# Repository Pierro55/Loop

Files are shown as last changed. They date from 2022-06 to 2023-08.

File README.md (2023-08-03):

# Loop Automatization Mod

<p align="center">
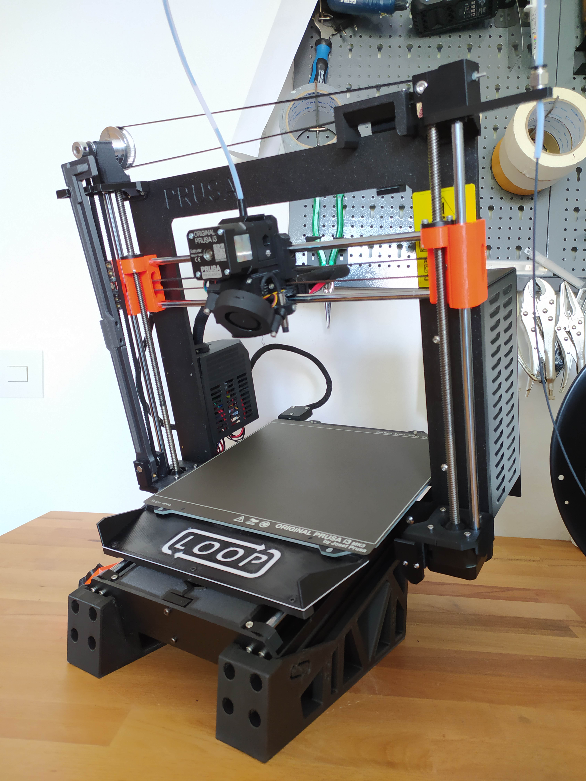
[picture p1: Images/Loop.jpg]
	
</p>

With this modification for the original Prusa MK3S+ you can put your 3D printer on autopilot and enable continuous printing. 

You can see the first version of the mechanism working in the following video:

https://user-images.githubusercontent.com/57869093/173814733-19abccf8-62e7-46f5-b48e-6825817a073e.mp4

For more detailed information check out the instruction section.

Feel free to join my Discord server for discussions and realtime updates: https://discord.gg/uEcjAfGHGe

If you are planning to build this mod, I would really appreciate it if you could post your progress on my Discord channel :)

### Credits
- Thanks to [Jonathan Kayne](https://grabcad.com/library/prusa-i3-mk3-solidworks-1) for providing the base model of the Prusa MK3
- Thanks to [smartin015](https://plugins.octoprint.org/plugins/continuousprint/) for providing the continuous print queue plugin
- Thanks to the [Octoprint team](https://octoprint.org/download/) for providing such incredible software
- I got some inspiration from [3D Que](https://www.3dque.com/) which got me motivated to build an improved system

Loop 3D printing automatisation now is integrated into [SimplyPrint](https://simplyprint.io/)

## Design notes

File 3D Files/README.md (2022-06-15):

# 3D Printing instructions
 
All STL-files are orientated in the correct orientation, just throw them into your slicer and off you go.

No support needed.

Depending on your setup (enclosure, printer on the table...) use at least PETG as material, ABS or PC would be even better.

Parts should have at leats 3-5 perimeters and 30% infill.

I printed all parts with a 0.6mm nozzle and 0.3mm layer height.

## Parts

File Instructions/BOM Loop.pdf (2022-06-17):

BOM Loop

Amount | Description | Comment | Links (DE)
2 | GT2 20T 8mm Bore Pulley | with set screws for shaft clamping | https://www.roboter-bausatz.de/p/rie (https://www.roboter-bausatz.de/p/riemenscheibe-gt2-20-zaehne-8mm-bohrung-fuer-6mm-riemen)
1 | GT2 20T Toothed Idler 5mm Bore | with bearing | https://www.roboter-bausatz.de/p/gt (https://www.roboter-bausatz.de/p/gt2-riemenscheibe-20-zaehne-5mm-bohrung-mit-dual-kugellager)
1 | GT2 60T 8mm Bore Pulley | with set screws for shaft clamping | https://www.roboter-bausatz.de/p/gt (https://www.roboter-bausatz.de/p/gt2-riemenscheibe-60-zaehne-8mm-bohrung-fuer-6mm-zahnriemen)
1 | 72cm GT2 Belt | Top Belt | https://www.roboter-bausatz.de/p/yo (https://www.roboter-bausatz.de/p/yourdroid-gt2-zahnriemen-offen-6mm-1-meter-faserverstaerkt)
1 | 69cm GT2 Belt | Belt Ejector Arm | https://www.roboter-bausatz.de/p/yo (https://www.roboter-bausatz.de/p/yourdroid-gt2-zahnriemen-offen-6mm-1-meter-faserverstaerkt)
1 | 52.5mm (stainless) steel rod | Shaft Top | https://www.dold-mechatronik.de/Pr (https://www.dold-mechatronik.de/Praezisionswelle-8mm-h6-geschliffen-und-gehaertet-Material-CF53-Zuschnitt)
1 | 31.5mm (stainless) steel rod | Shaft Bottom | https://www.dold-mechatronik.de/Pr (https://www.dold-mechatronik.de/Praezisionswelle-8mm-h6-geschliffen-und-gehaertet-Material-CF53-Zuschnitt)
1 | 62cm PTFE Tube OD 4mm | Reverse Bowden Feed-in | https://www.roboter-bausatz.de/p/1- (https://www.roboter-bausatz.de/p/1-meter-ptfe-schlauch-3-mm-x-4-mm-fuer-bowden-extruder)
1 | M6 PTFE Bowdencoupler | Reverse Bowden Feed-in, Push through type | https://www.roboter-bausatz.de/p/pc (https://www.roboter-bausatz.de/p/pc4-m6-bowden-schnellverbinder-straight-through)
17 | M3 Heat inserts | d1 Ø4,6mm; d2 Ø3,9mm; L5,7 --------------->>>>> | https://www.amazon.de/ruthex-Gewi (https://www.amazon.de/ruthex-Gewindeeinsatz-St%C3%BCck-Gewindebuchsen-Kunststoffteile/dp/B08BCRZZS3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)
5 | M3 Nut | 3x Ejector Lip + 2x Belt Idler Top
3 | M3x6 | Ejector Lip screws
14 | Button Head M3x10
1 | M3x16 | Ejector arm clamp screw
2 | M3x18 | GT2 Belt tensioner
1 | M3x30 | Top Belt Idler tensioner
1 | M5x16 | Top Belt Idler GT2 Idler "Shaft"
6 | M5x10 | Feet + Mechanics Cover
6 | Hammernut Slot 8 Type I | Feet + Mechanics Cover | https://www.ebay.de/itm/273816981 (https://www.ebay.de/itm/273816981652?var=574480277127)
1 | Square Nut M5 (8x8x2,7mm) | Top Belt Idler GT2 Idler, use some Loctite 243 to secure the bolt | https://www.ebay.de/itm/113023762 (https://www.ebay.de/itm/113023762539)
4 | Countersunk Wood screw 3x10mm | GT2 Belt tensioner --------------->>>>> | https://www.amazon.de/SPAX-Schrau (https://www.amazon.de/SPAX-Schrauben-Senkkopf-PZ-Vollgewinde-10/dp/B007259QA6)

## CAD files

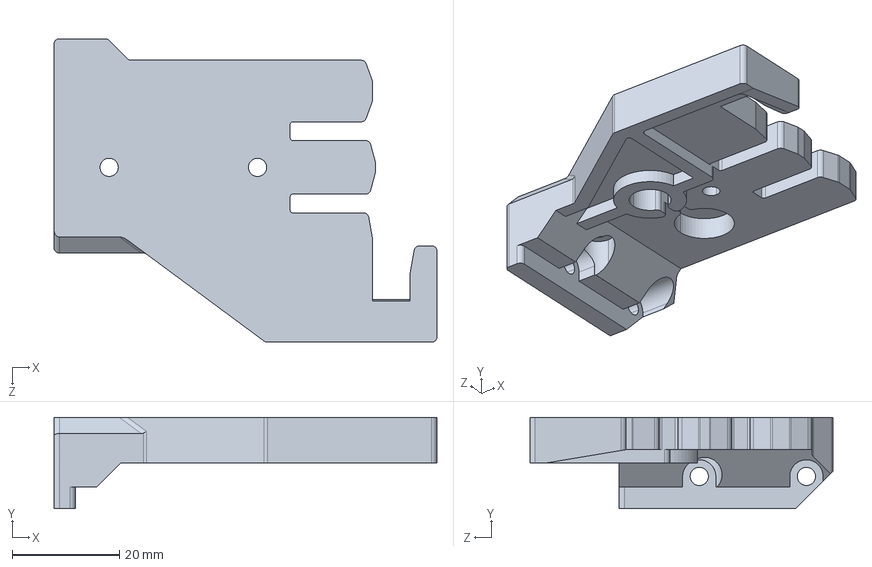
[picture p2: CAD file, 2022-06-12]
3D Files/STEP/Z_Axis_Top_LEFT.STEP
71.5 x 17.0 x 56.6 mm

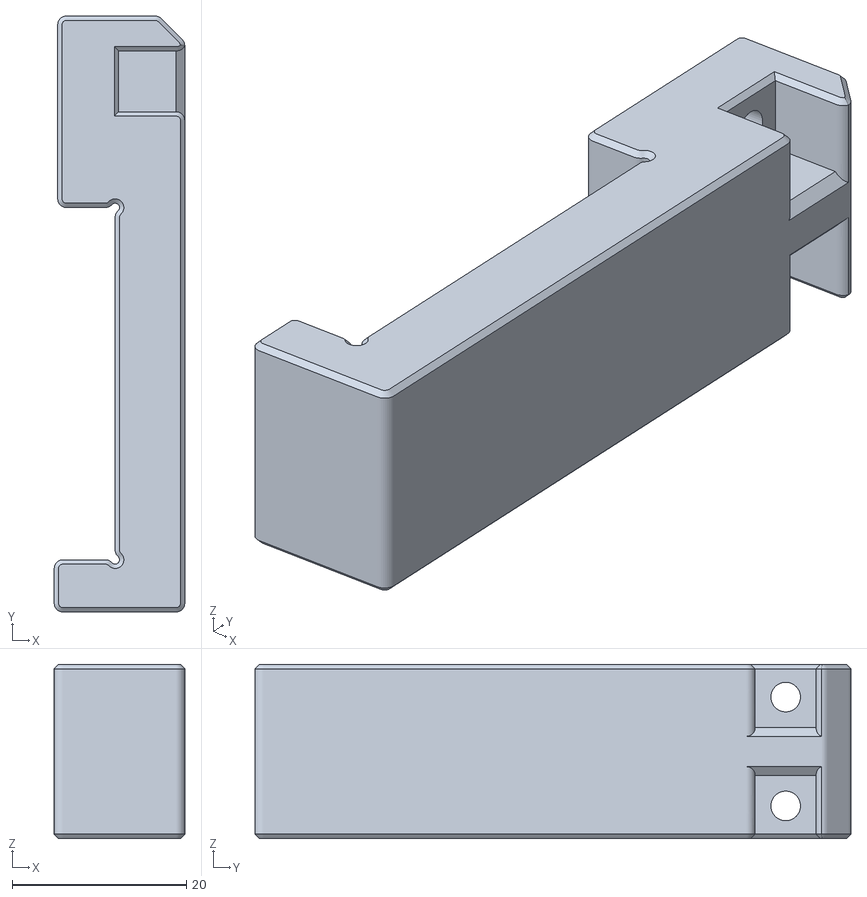
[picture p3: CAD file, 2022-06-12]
3D Files/STL/Mechanism gripper Part 2.stl
15.0 x 68.5 x 20.0

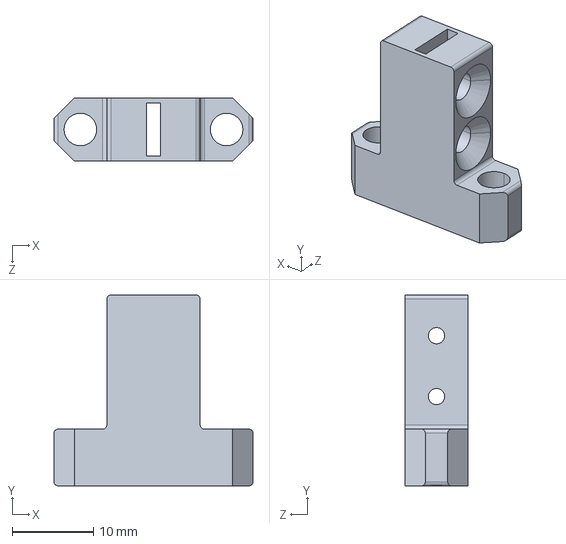
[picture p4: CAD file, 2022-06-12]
3D Files/STEP/GT2 Belt tensioner 2.STEP
24.5 x 23.5 x 7.75 mm

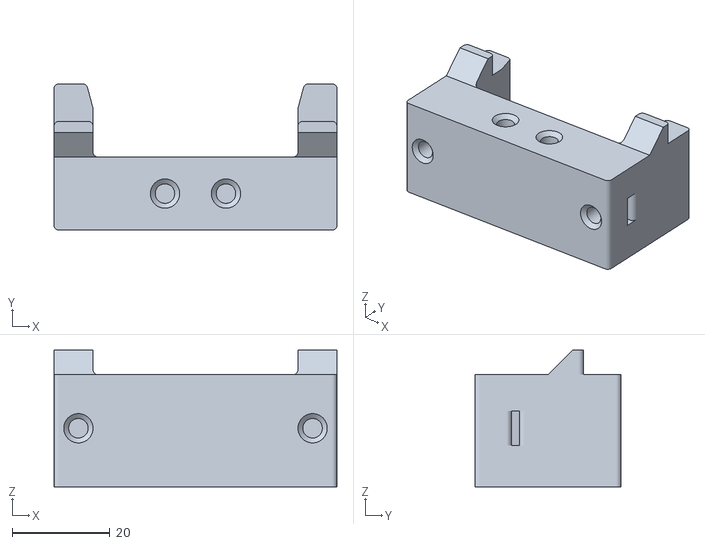
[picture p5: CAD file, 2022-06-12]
3D Files/STL/Mechanism gripper Part 1.stl
58.0 x 30.0 x 28.0

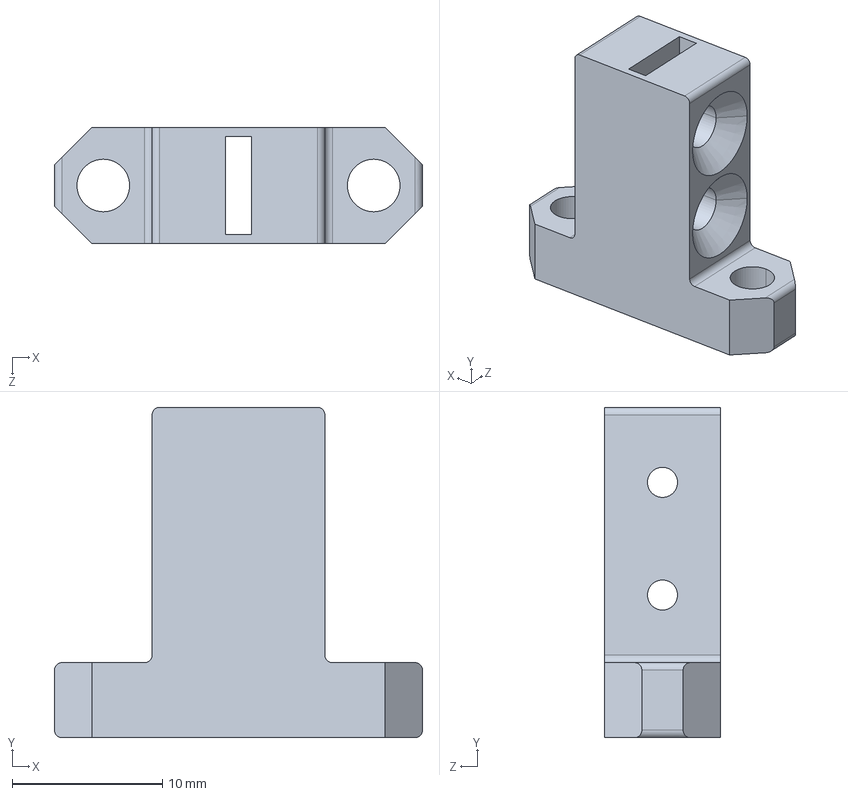
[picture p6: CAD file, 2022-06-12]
3D Files/STEP/GT2 Belt tensioner 1.STEP
24.5 x 22.0 x 7.75 mm

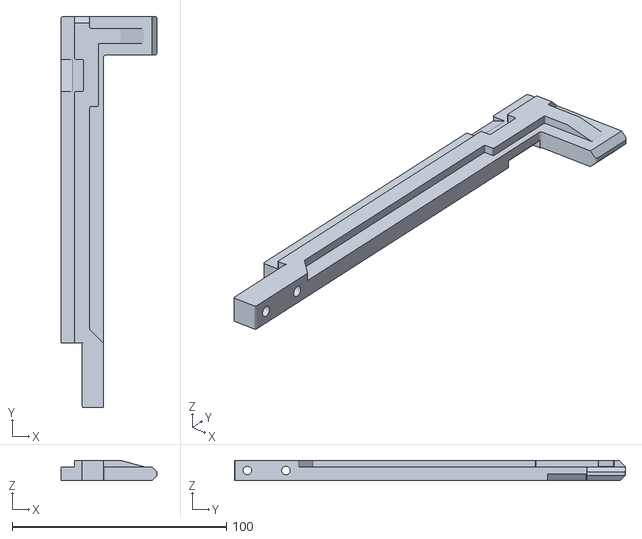
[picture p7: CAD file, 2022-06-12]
3D Files/STL/Ejection arm Part 1.STL
45.0 x 182.5 x 9.50

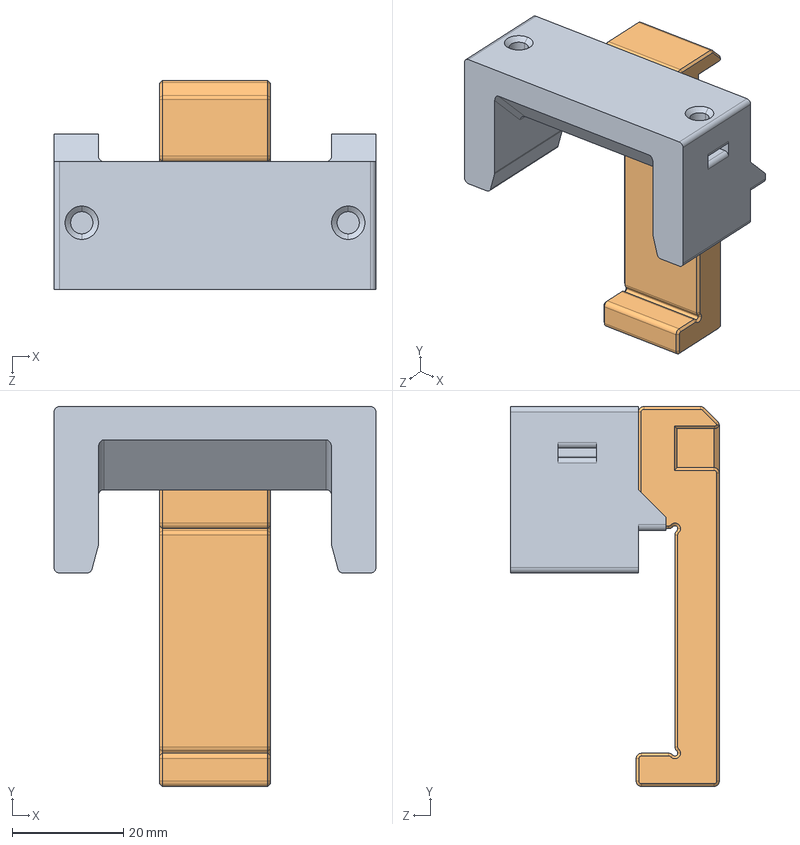
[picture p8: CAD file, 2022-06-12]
3D Files/STEP/Mechanism gripper.STEP
58.0 x 68.5 x 37.6 mm

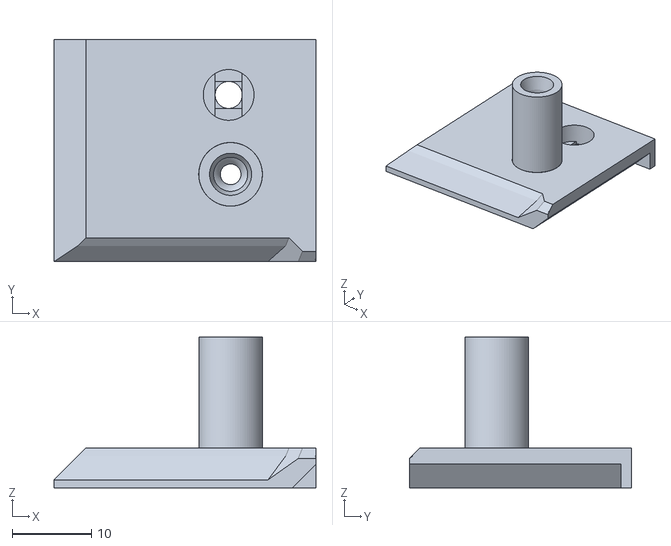
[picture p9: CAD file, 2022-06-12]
3D Files/STL/fs-cover-PTFE Tube Adapter.stl
33.0 x 28.0 x 19.0

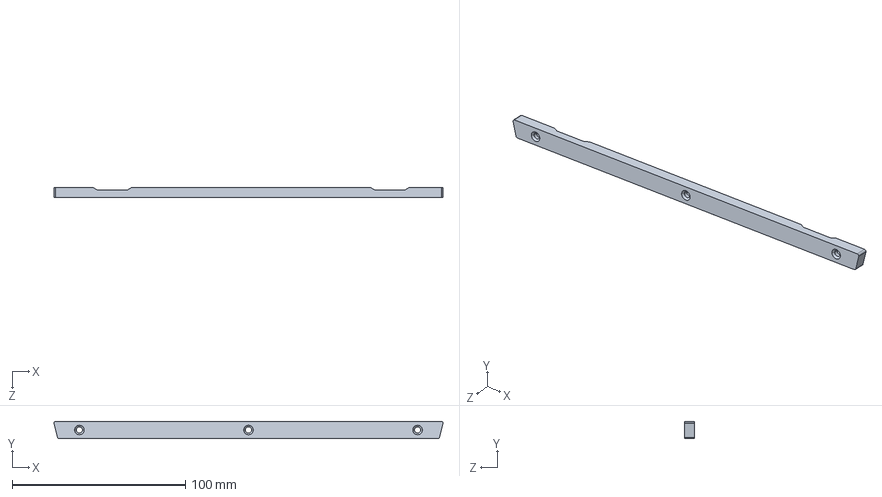
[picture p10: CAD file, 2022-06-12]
3D Files/STEP/Ejector blade lip.STEP
224.3 x 10.0 x 6.00 mm

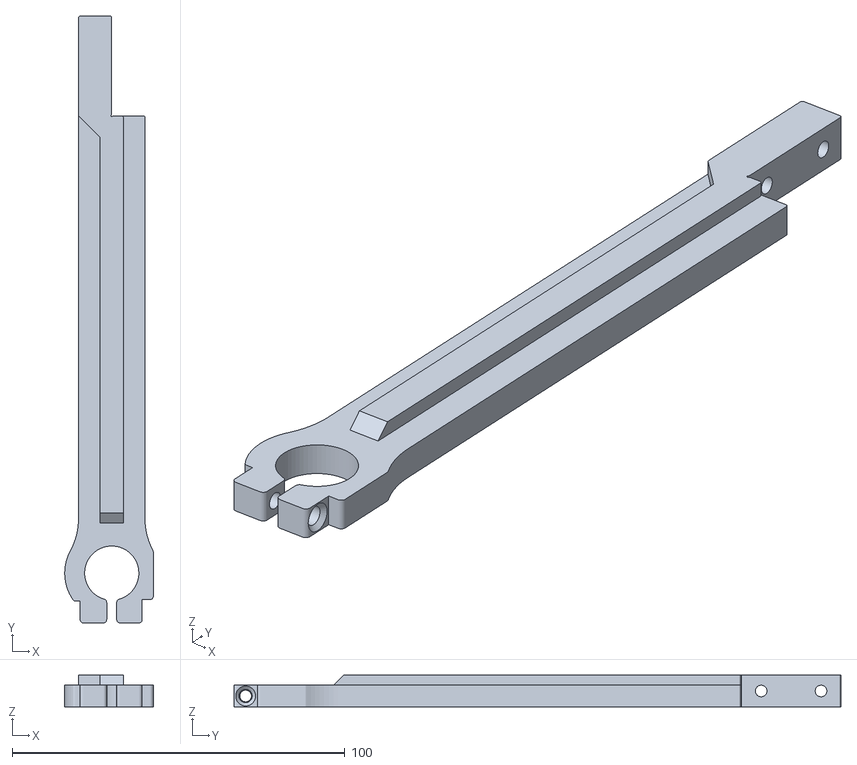
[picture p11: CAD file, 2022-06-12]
3D Files/STL/Ejection arm Part 2.STL
26.6 x 182.5 x 9.50

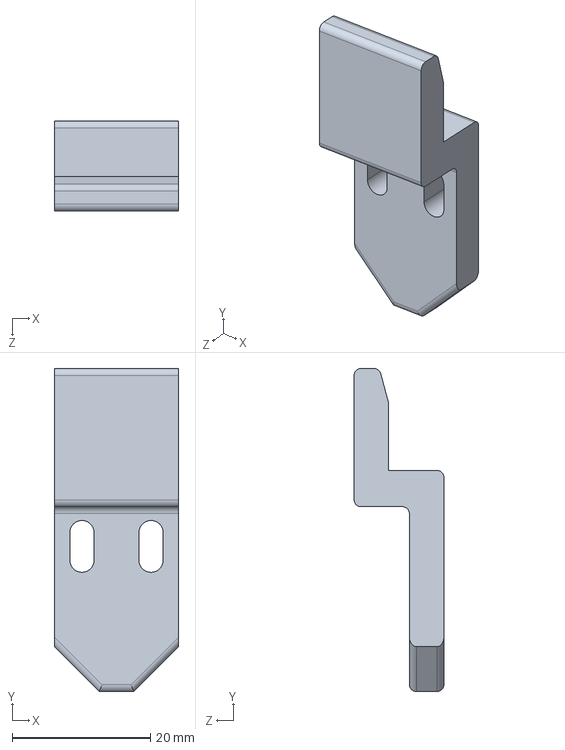
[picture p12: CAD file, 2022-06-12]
3D Files/STEP/Ejection arm endstop.STEP
18.0 x 46.8 x 13.0 mm

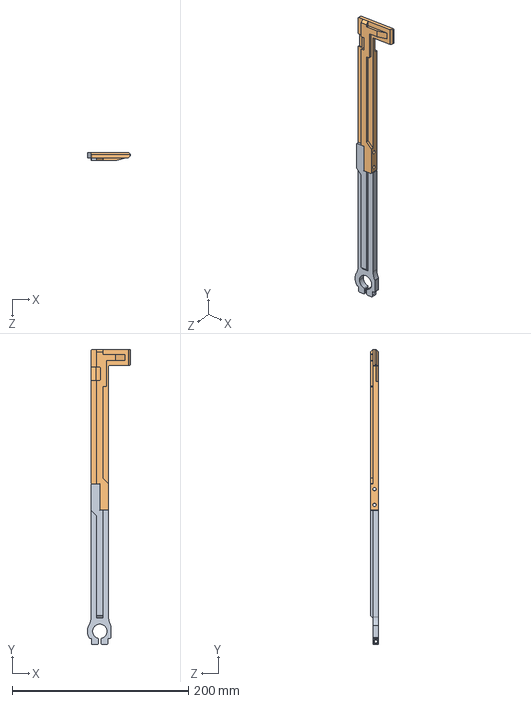
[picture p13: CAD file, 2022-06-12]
3D Files/STEP/Ejection arm.STEP
49.1 x 335.0 x 9.50 mm

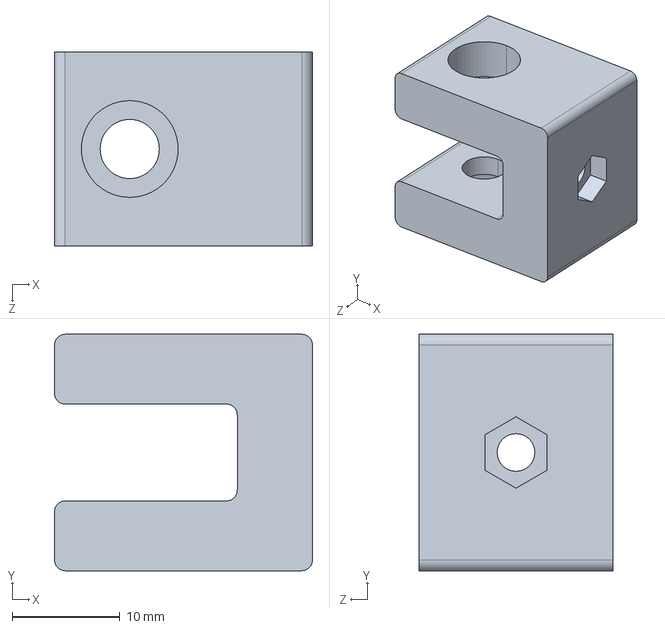
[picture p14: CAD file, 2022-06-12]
3D Files/STEP/Belt_Idler_top_RIGHT.STEP
24.0 x 22.0 x 18.0 mm

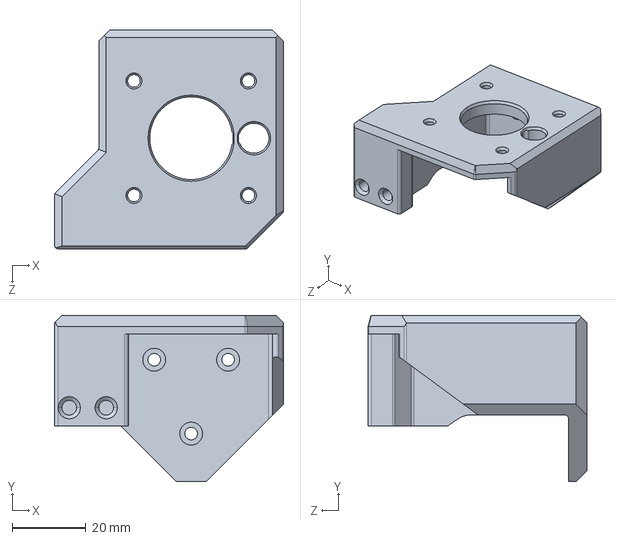
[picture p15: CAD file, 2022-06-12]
3D Files/STEP/Z_Axis_Bottom_RIGHT.STEP
62.0 x 45.0 x 59.3 mm

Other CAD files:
3D Files/STEP/Ejector blade blank.STEP
3D Files/STEP/Bearing_block_TOP.STEP
3D Files/STEP/Bed mechanics cover MIRROR.STEP
3D Files/STEP/Belt_tensioner_top_RIGHT.STEP
3D Files/STEP/Bed mechanics cover.STEP
3D Files/STEP/Ejection arm pivot point.STEP
3D Files/STEP/Ejector blade.STEP
3D Files/STEP/Tilted foot MIRROR.STEP
3D Files/STEP/Tilted foot.STEP
3D Files/STEP/Z_Axis_Bottom_LEFT.STEP
3D Files/STEP/Z_Axis_Top_RIGHT_Filament_Guide.STEP
3D Files/STL/Bearing_block_TOP.stl
3D Files/STL/Bed mechanics cover MIRROR.stl
3D Files/STL/Bed mechanics cover.stl
3D Files/STL/Belt_Idler_top_RIGHT.STL
3D Files/STL/Belt_tensioner_top_RIGHT.STL
3D Files/STL/Ejection arm endstop.stl
3D Files/STL/Ejection arm pivot point.STL
3D Files/STL/Ejector blade blank.stl
3D Files/STL/Ejector blade lip.stl
3D Files/STL/Ejector blade.stl
3D Files/STL/GT2 Belt tensioner 1.STL
3D Files/STL/GT2 Belt tensioner 2.STL
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

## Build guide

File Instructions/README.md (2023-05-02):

# Loop Instructions

## Important information (please read carefully)

- Calibrate your Z-offset to get a good first layer (too close to the bed makes the prints adhere more which we don't want)
- Choose the right material and brand. The quality from various vendors can differ, make sure to test new materials first (even if they are the same material type). Join my document on different material types --> [Material Data](https://docs.google.com/spreadsheets/d/1ghuwrelvSEJ2hHmYuEMqaSpLGjrf1bYgRo76JcQ4j_E/edit?usp=sharing)
- Calibrate the first layer temperature --> lower temperatures make the part stick less to the buildplate which we want
- Use the textured PEI spring steel sheet from Prusa (depending on the batch number, you might get different results)
- Make sure to wash your buildplate with dish soap every once in a while, and to not use any adhesives on the bed itself. 
- Disable crash detection mode as it will not work properly due to the tilted frame
- If you use a skirt, set the skirt height in the slicer to a minimum of 6 layers and the skirt offset to 0,5mm

Want to test if the system works before building it?

- Clean your buildplate with water and dish soap
- Print something
- Let it cool down to 30°C
- If it releases easily, Loop can handle it. If not, try some of the suggestions from above. 

## Build instructions

What worked best for me:

**a)** Insert all brass heat inserts (see [Heat_Inserts.pdf](https://github.com/Pierro55/Loop/blob/main/Instructions/Heat%20Insert%20Locations.pdf) for more information)

**b)** Mount the following parts beforehand:
- Belt tensioner Top RIGHT ++ Z-Axis Top RIGHT ++ M6 PTFE coupler
- Bearing block TOP ++ Z Axis Top LEFT
- Ejection arm pivot point ++ Z Axis Bottom LEFT
- Ejection arm endtstop ++ Z Axis Bottom RIGHT (only pre-tighten for now)
- Ejector arm part 1 ++ Ejector arm part 2
- Ejector blade ++ Ejector lip
- Top axis ++ Bearing block TOP ++ GT2 60T 8mm pulley ++ GT2 20T 8mm as shown in the picture below (without the belts)

<p align="center">
	
</p>

**c)** Assembly instructions

1) Move the Z-Axis to 190mm via the LCD and fix the X-gantry with tape or zip ties to the frame

2) Unplug and unscrew the LCD first while laying the machine on the PSU side, mount the mechanics cover and the feet, flip the machine around afterwards

3) Cut the zip ties from the Z-motor cables --> unscrew the Z-axis motor mounts --> unscrew the Z-axis rod --> unscrew the Z-axis brackets and change them with 		the mod parts --> reverse all steps

4) Cut the zip ties/tape from the X-gantry --> move the Z-Axis down manually roughly to the middle position --> unscrew all top parts and change them with the mod parts (including the mechanism gripper)
	
5) Mount the top belt first --> tighten the loose ends with the top screw of the mechanism gripper --> make sure that the Belt Idler top RIGHT does not 		interfere with the mechanism gripper when the gripper is on its idle position (see picture below) --> tighten the Belt Idler top RIGHT until the belt has 	reasonable tension (**Notice: The idle position of the mechansim gripper is flat against the Z_Axis_top_RIGHT part**)
<p align="center">
	
</p>	

6) Mount the ejector arm --> slide the mounted ejector arm over the GT2 20T 8mm bore pulley so that it sits where the GT2 belt would normally be located (set screws are accessible) --> insert that into the ejection arm pivot point and slide the 8mm shaft in from the outside --> tighten the setscrews --> slide the ejector arm over the set screws of the GT2 Pulley and tighten the clamp of the arm

7) Mount the vertical ejector belt --> slide the 69cm belt thorugh the pivot point and the GT2 pulley (teeth side of the belt facing the teeth of the pulley) --> mount the GT2 belt tensioner 1+2 att each on end of the belt (orientation doesn't matter) --> lay one end around the upper pulley --> connect the two tensioners via two M3x18mm screws --> tighten the screws until the belt has reasonable tension

8) Mount the LCD either to the left or right side of the machine

9) Mount the ejector blade (with mounted lip) --> remove the spring steel sheet --> unscrew the first row of screws, 3 in total --> use a plier to remove the spacers between the buildplate frame and heater PCB --> insert the ejector blade (make sure that the faces of the ejector blade which will be sandwiched in between the frame and the PCB are flat, if not sand them smooth) and align the holes with the PCB heater --> mount the screws of the PCB heater, tighten the middle one first after inserting all 3 screws --> put the spring steel sheet back on top of the PCB heater

10) Replace the filament sensor cover with the modded version --> insert the PTFE tube into the coupler and the filament sensor cover (let roughly 30mm poke out the other end of the coupler so that filament can be inserted more easily 

11) Calibrate the system --> loosen the top GT2 20T pulley --> move the ejector arm the the outermost left position (idle position) --> move the mechanism gripper to its idle position and move it back about 1-2mm --> tighten the set screws of the top pulley --> move the mechanism gripper to its idle positon by hand --> perform a Z-Axis calibration via the LCD

12) Calibrate the ejector arm endstop --> run [Calibrate e-arm endstop.gcode](https://github.com/Pierro55/Loop/blob/main/Instructions/Calibrate%20e-arm%20endstop.gcode) --> after the printer beeps, adjust the ejector arm endstop height so that the arm is parallel to the buildplate --> tighten the screws of the ejector arm endstop --> click the encoder wheel on the LCD and let the Gcode finish

To check if everything is installed and calibrated correctly please run [Demo Loop.gcode](https://github.com/Pierro55/Loop/blob/main/Instructions/Demo%20Loop.gcode). This will run the ejection sequence. 

## Adding a printing queue

For full functionality you need a Raspberry Pi or something else that can run Octoprint. 
I suggest using a raspberry Pi zero 2W because you can install it directly onto the Prusa motherboard. 

Here are the instructions for installing a raspberry Pi zero 2W [Instructions RPI Zero](https://help.prusa3d.com/article/prusaprint-rpi-zero-and-octoprint_2180). The instructions are for a Raspberry Pi zero but it is the same for the zero 2W.

If you are using a different SBC, here are instructions on how to get Octoprint running [Instructions Octoprint](https://octoprint.org/download/)

Next, download the [continuous print queue plugin](https://plugins.octoprint.org/plugins/continuousprint/)

After these steps continue with the slicer settings and you should be good to go!
You can add the Gcode below of the automation sequence to the continuous print queue plugin but I recommend having it in the slicer settings as seperate printer profile.

## Slicer Settings
Because of the way this modification is designed, some build volume is lost
- Change the buildvolume to Y-max 185mm and Z-max 194mm (Printer Settings --> General --> Bed shape for Y-setting, Max print height for Z-setting)

You can still print the whole X and Y volume if you just print with a normal Prusa printer profile. Make sure to limit the Z-axis to 194mm. I suggest saving a seperate "Printer Setting" if you wish to print bigger occasinally with the mod disabled.

### Copy the following Gcode to your Start Gcode in Prusa Slicer (Printer Settings --> Custom G-code --> Start G-code)
```
M862.3 P "[printer_model]" ; printer model check
M862.1 P[nozzle_diameter] ; nozzle diameter check
M115 U3.10.1 ; tell printer latest fw version
G90 ; use absolute coordinates
M83 ; extruder relative mode
G28 W ; home all without mesh bed level
G1 Z20 F1000 ;raise Z axis
G1 Y212 F10000 ;move bed to idle position
;M140 S[first_layer_bed_temperature] ; set bed temp
M190 S[first_layer_bed_temperature] ; wait for bed temp
M109 S170 ;wait for extruder temp for ABL
G80 ; mesh bed leveling
G1 Z15 F1000 ;raise Z axis
M104 S[first_layer_temperature] ; set extruder temp
M109 S[first_layer_temperature] ; wait for extruder temp

;----Intro line sequence------
G1 Z0.2 F720 ;raise Z axis
G1 Y-3 F1000 ; go outside print area
G92 E0 ;zero extruder
G1 X80 F10000 ; move X-axis
G1 E5 F1000; prime the nozzle
G1 X180 E21 ; intro line
G1 Z0.4 F720 ;raise Z axis
G1 X80 E21 F1000 ; intro line
G1 Z0.8 F720 ;raise Z axis
G1 X180 E21 F1000 ; intro line
G1 Z1.2 F720 ;raise Z axis
G1 X80 E21 F1000 ; intro line
G1 Z1.6 F720 ;raise Z axis
G1 X180 E21 F1000 ; intro line
G1 Z2 F720 ;raise Z axis
G1 X80 E21 F1000 ; intro line
G1 X70 F10000 ; quickly move away from intro line
G1 E-0.8 ;retract
G92 E0 ;zero extruder
;--------------------------------------

M221 S{if layer_height<0.075}100{else}95{endif}
```

### Copy the following Gcode to your End Gcode in Prusa Slicer (Printer Settings --> Custom G-code --> End G-code), make sure to change the release temperature according your needs
```
G1 E-6 F1000 ;retract
G4 ; wait
M221 S100 ; reset flow
M900 K0 ; reset LA
{if print_settings_id=~/.*(DETAIL @MK3|QUALITY @MK3|@0.25 nozzle MK3).*/}M907 E538 ; reset extruder motor current{endif}
M104 S0 ; turn off temperature
M107 ; turn off fan
G1 Y212 F10000 ; move Y-axis
{if max_layer_z < max_print_height}G1 Z{z_offset+min(max_layer_z+5, max_print_height)}{endif} ; Move print head up

;-----Automatic ejection sequence------
M190 R32 ; wait for bed temp !!CHANGE THIS TO YOUR SPECIFIC RELEASE TEMPERATURE!!
G1 X245 F7000 ; move X-axis
G1 Z210 F1500 ; raise Z-axis
M907 Y800 X800 ; increase Y+X-motor current temporarily
G1 X210 F800 ; move X-axis

; wiggle motion
G1 Y-4 F2500 ; move Y-axis
G1 Y210 F20000 ; move Y-axis
G28 Y ;home Y to knock off lose objects
G28 Y ;home Y to knock off lose objects
G28 Y ;home Y to knock off lose objects
G1 Y-4 ; move Y-axis
G1 Y155 ; move Y-axis

G1 X247.5 F800 ; move X-axis
M907 Y540 X540 ;reset Y+X-motor current
G1 Z50 F1000 ; lower Z-axis
G1 X125 Y212 F10000 ; move X-axis
;--------------------------------------

M140 S0 ; turn off heatbed
M84 ; disable motors
```

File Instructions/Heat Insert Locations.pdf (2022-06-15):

## Heat Insert Locations

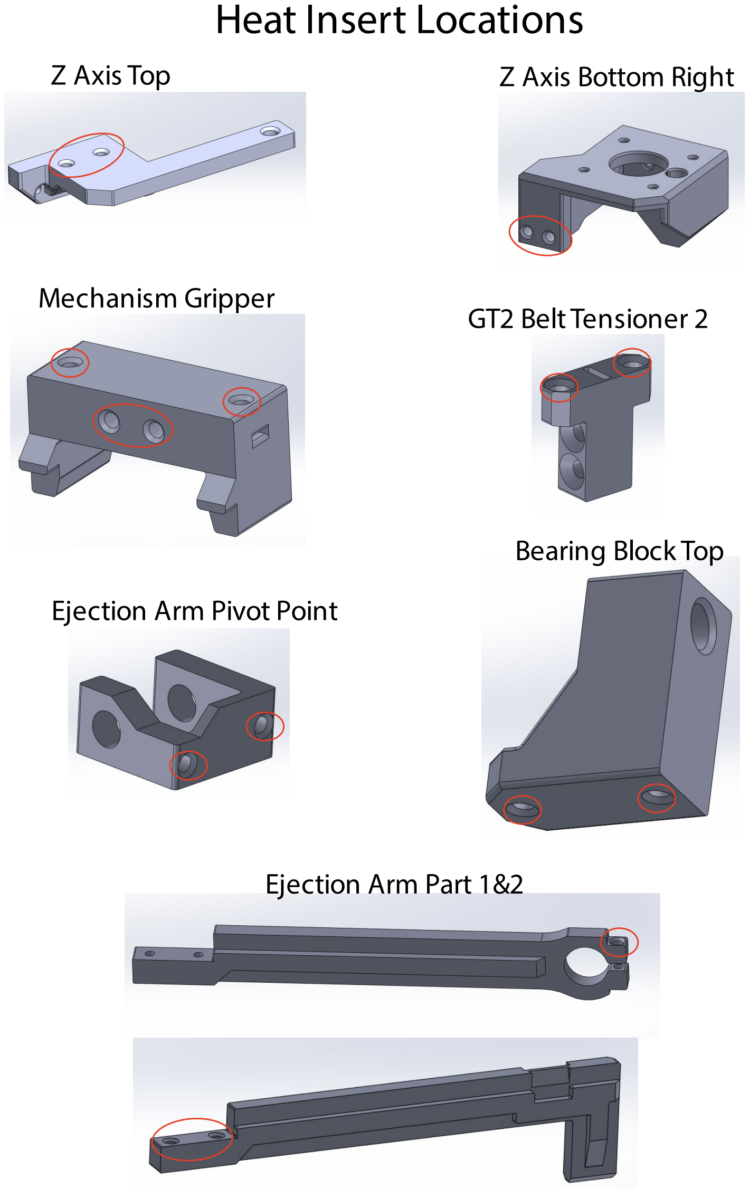
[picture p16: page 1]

Z Axis Top | Z Axis Bottom Right
Mechanism Gripper | GT2 Belt Tensioner 2

Ejection Arm Pivot Point

Bearing Block Top

Ejection Arm Part 1&2

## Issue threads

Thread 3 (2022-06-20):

Get rid of the horizontal belt

DomML, 2022-06-20:
Hello.
First off, it's a very nice project, and I seriously consider to replicate it.
I was wondering if I would be possible to remove the horizontal axis at the top to only keep the vertical one (on the side), where the part interacting with the extruder would be located.
I believe this would simplify the design, but there may be a reason you didn't did it like that?
Still, great project,
DML.

Pierro55, 2022-06-20:
This would probably make the design more complex as you have to avoid the X-axis part on the left and you would probably lose even more Z-height because you have to move the extruder down to move the ejector arm. The ejector arm would also collide with the extruder. You would have to place the arm and the mechanism at the back of the printer which might lead to not being able to push prints all the way off the buildplate.

These are the thing that come spontaneously to my mind but feel free to remix the system. You can find the STEP files in the 3D files folder.

DomML, 2022-06-20:
Nice thanks!

Closed 2022-06-20.

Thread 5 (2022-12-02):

Bed mechanics cover blocks movement

Kertonix, 2022-12-02:
Bed mechanics cover blocks movement of the bed towards front.
Because of it belt test cannot be completed.

Pierro55, 2022-12-02:
Hey Kertonix,
can you please post a picture of how you mounted the cover?

Pierro55, 2022-12-02:
> Hey Kertonix,
> can you please post a picture of how you mounted the cover?

Kertonix, 2022-12-05:
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

Pierro55, 2022-12-05:
@Kertonix Thanks
I've just run the belt test (Prusa setting) on my machine and it worked just fine.
Checked the CAD model as well and nothing is colliding anywhere:
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

But what I've noticed on your setup, you have the old version of the Y-rod holder. Do you have a MK3S instead of a MK3S+?
Maybe they've changed the belt tensioner for the Y-axis as well.

If that does not solve the problem, could you please post a video of the problem (maybe put the printer on its side and film the underside of the y bed while it is moving)?

Kertonix, 2022-12-12:
Cutting thickening of "Bed mechanics cover MIRROR" lip did the job.
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

Kertonix, 2022-12-12:
It came from cutting (with knife and hot-air)

Closed 2022-12-12.

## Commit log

2022-06-12 Adding 3D Files
    [Bearing_block_TOP.STEP, Bearing_block_TOP.stl, Bed mechanics cover MIRROR.STEP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]
2022-06-12 Revert "Delete Loop Assembly.STEP"
    This reverts commit a65a47008fc0c3f3df835f33d557db4fd5adc366.
2022-06-15 BOM upload
    [BOM Loop.xlsx]
2022-06-15 BOM Loop PDF file
    [BOM Loop.xlsx]
2022-06-15 BOM updated
    [BOM Loop.xlsx]
2022-06-15 Added Heat Insert Locations PDF
2022-06-17 added links (DE)
    [BOM Loop.xlsx]
2022-06-20 added demo and calibration gcode
2022-06-20 Update Calibrate e-arm endstop.gcode
